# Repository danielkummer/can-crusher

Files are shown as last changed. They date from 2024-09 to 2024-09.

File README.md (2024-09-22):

# Can Crusher

This can crusher uses a liner motor to slowly but surely crush your tin can.

## Bill of Materials

### Screws
* 17x M3 screws (different lengths)
* 10x M4 screws 10mm
* 4x M5 screws 15mm

### Hardware
* 1x Linear shaft
* 1x Stepper motor with gearbox
* 2x push button sensors
* 1x RGB LED push button
* 1x WS2811S led driver
* 1x stepper motor driver 2A
* 1x Arduino Nano every
* 1x 12V 2A power supply
* 1x power supply connector
* connection cables of different lengths

### Stepper Motor

You'll need a stepper motor with a gearbox to produce a lot of torque.
I've found one here: https://eu.robotshop.com/de/products/12v-17a-667-oz-in-nema-17-bipolarer-schrittmotor 

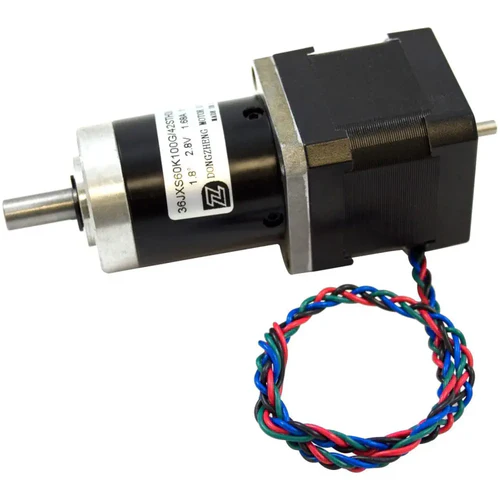
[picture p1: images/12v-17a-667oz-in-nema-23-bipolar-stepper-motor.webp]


It's a 12 V, 1,7 A, 667 oz-in NEMA-17 bipolar stepper motor with a 991044/2057 :1 planetary gear ratio.
The important metric however is the **48kg/cm torque** it can produce.

### Linear shaft

This will be a bit a hassle to find probably. I have found mine here: https://techstudio.ch/products/zeberoxyz-150mm-effektive-lnge-linear-schienenfhrung-kugelumlaufspindel-sfu1605-mit-nema17-schrittmotor-fr-diy-cnc-router-teile-x-y-z-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 

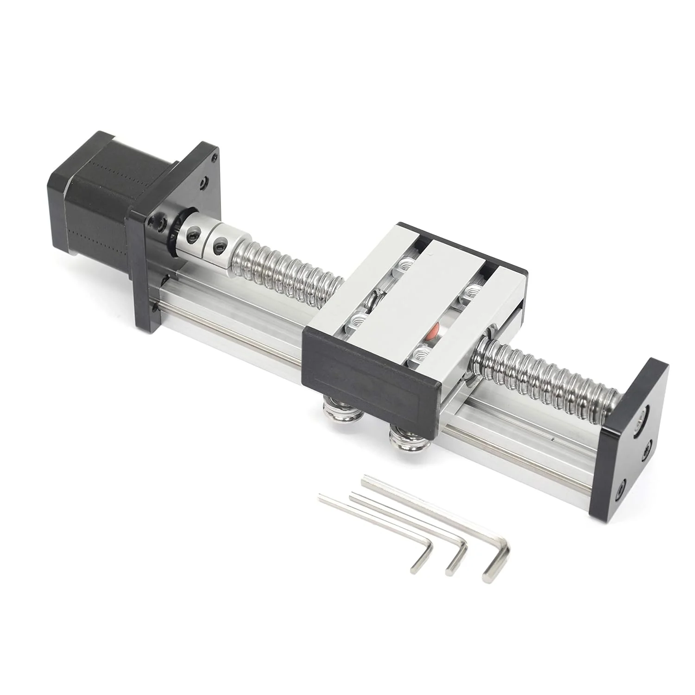
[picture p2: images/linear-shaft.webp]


It has an effective length of 150mm which should be enough for most normal sized tin cans.

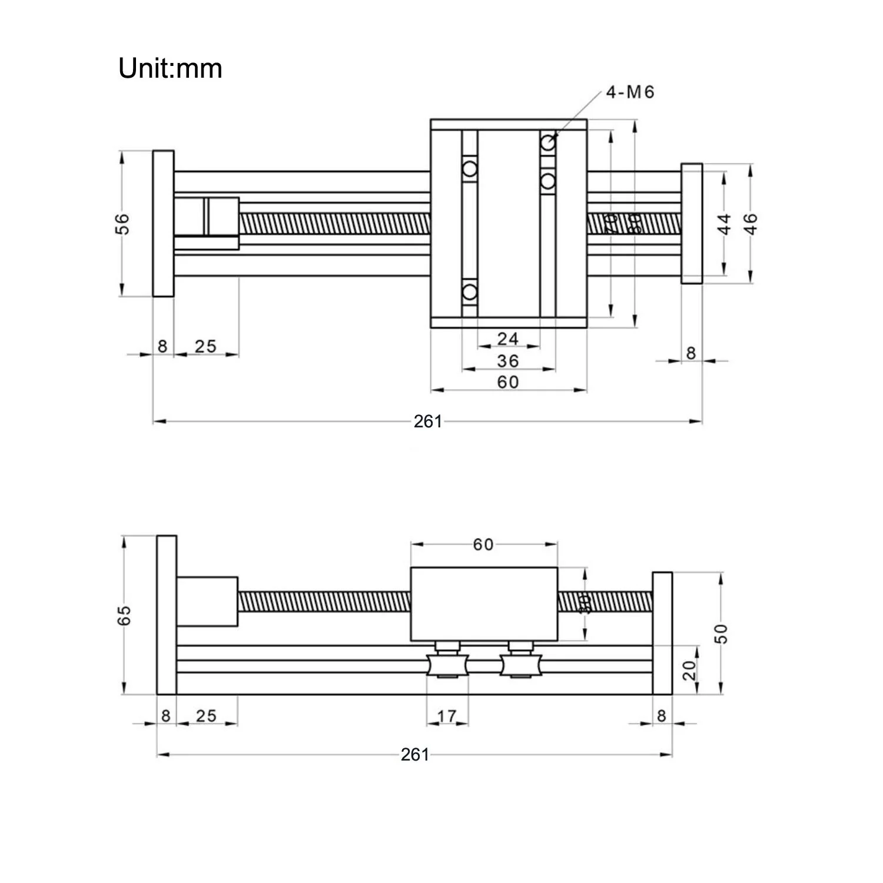
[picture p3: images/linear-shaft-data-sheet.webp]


The shaft came with a Nema 17 stepper motor but it was ungeared and way too weak.

### Push button

The push button is coming from adafruit: https://www.adafruit.com/product/3350 

Diameter: 16mm

### Sensors

I'm using a microswitch breakout board obtained here: https://www.play-zone.ch/de/microswitch-breakout-endstop-active-low.html

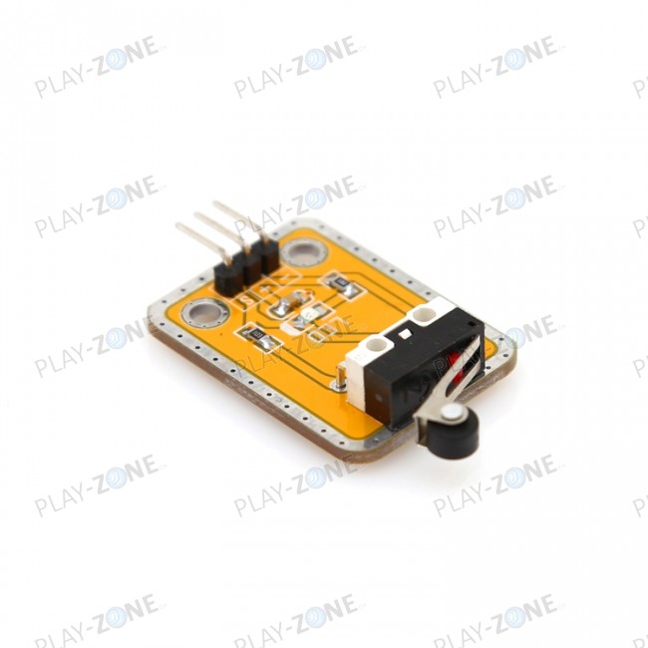
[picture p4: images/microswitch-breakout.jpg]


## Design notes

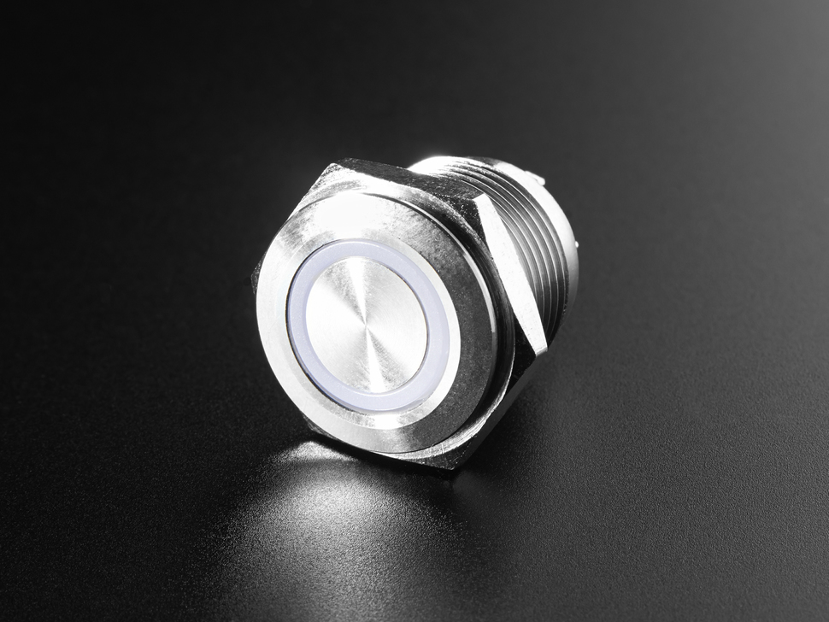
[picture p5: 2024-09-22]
images/metal-pushbutton.jpg

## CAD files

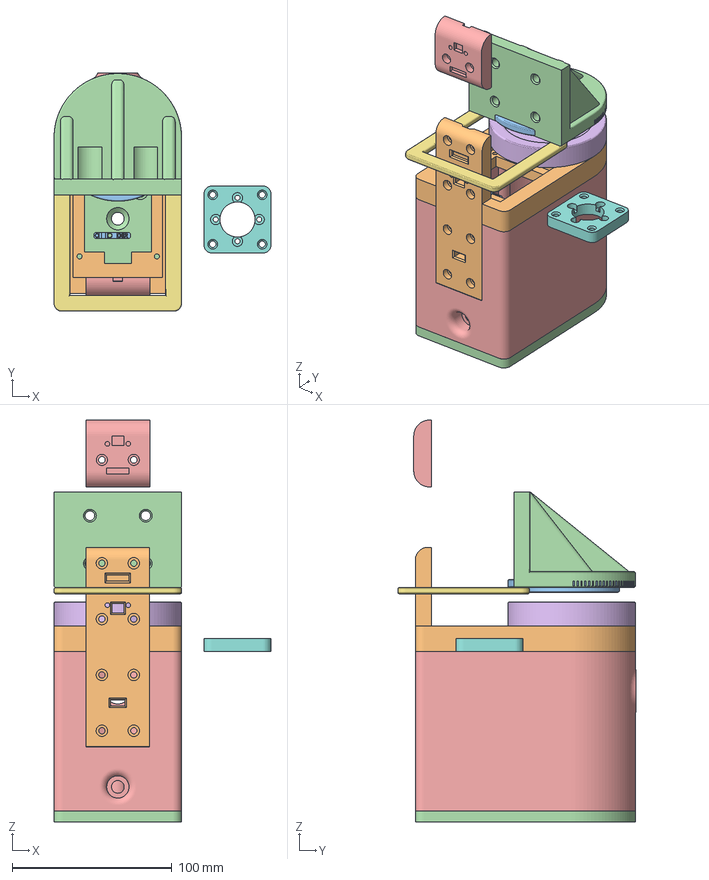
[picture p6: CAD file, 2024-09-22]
3d-files/CanCrusherWithLinerMotor.3mf
136.0 x 149.5 x 252.0 mm
ArduinoClamp
BackFastener
Bottom
Casing
CrusherPlate
CrusherPlateSensorBack
MotorAdapter
MotorDriverClamp
MotorMounting
Tag
TopCrusher
TopSensorHolder

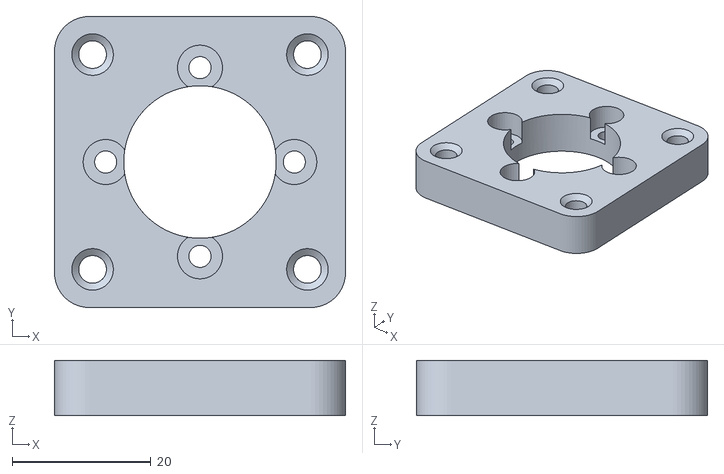
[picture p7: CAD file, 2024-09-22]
print-files/MotorAdapter.stl
42.0 x 42.0 x 8.00

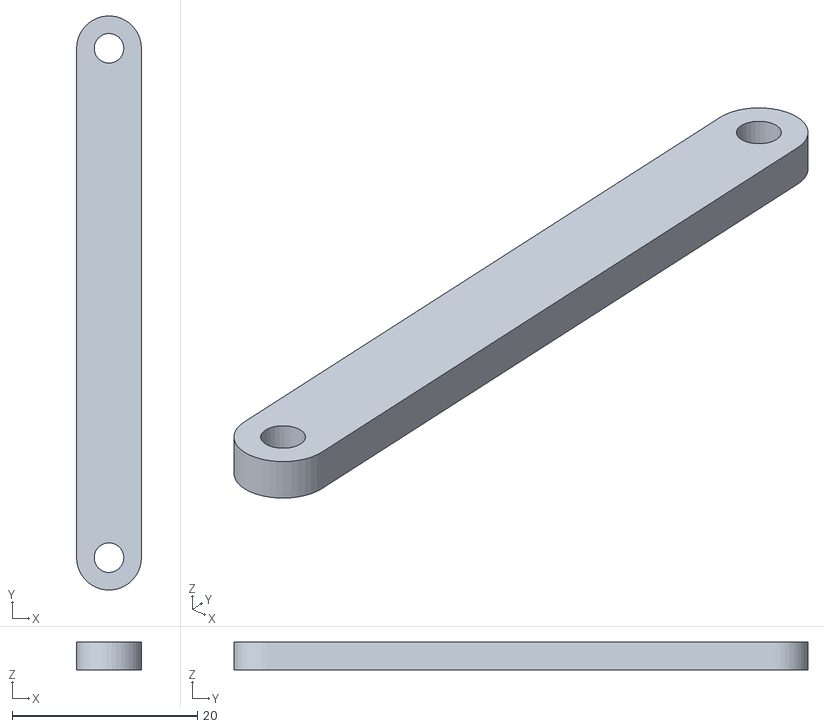
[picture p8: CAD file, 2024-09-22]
print-files/ArduinoClamp.stl
7.00 x 62.0 x 3.00

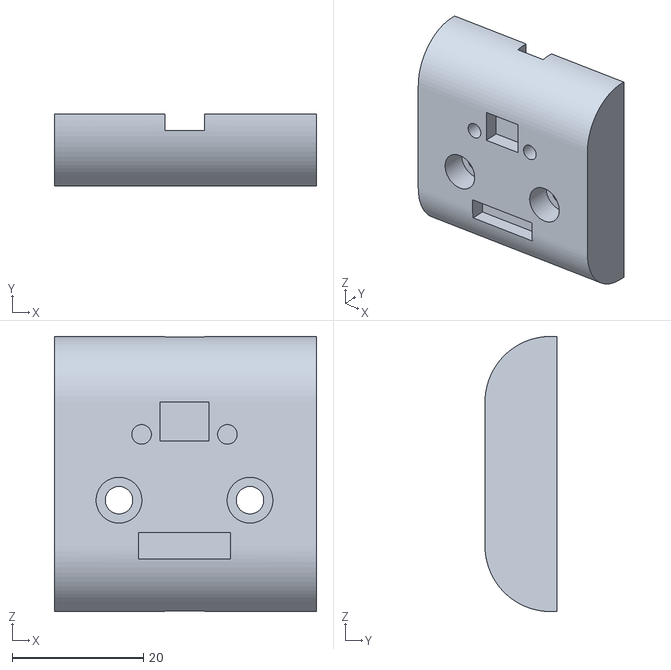
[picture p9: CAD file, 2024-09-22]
print-files/TopSensorHolder.stl
40.0 x 11.0 x 42.0

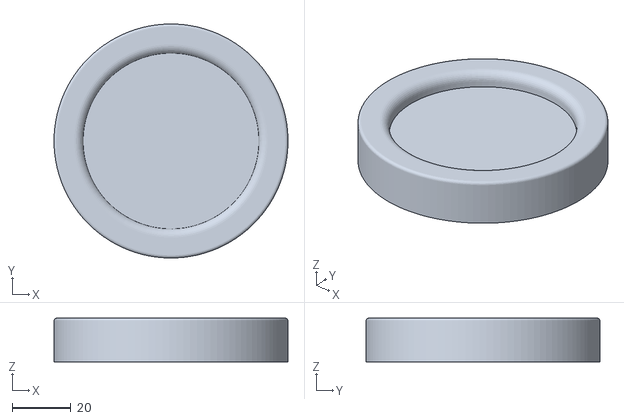
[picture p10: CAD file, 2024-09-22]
print-files/CrusherPlate.stl
80.0 x 80.0 x 15.0

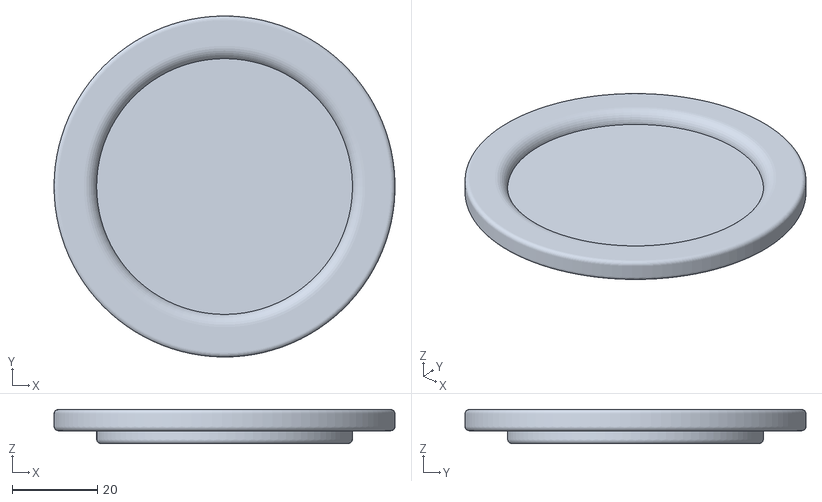
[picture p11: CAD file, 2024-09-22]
print-files/CrusherCup.stl
80.0 x 80.0 x 8.00

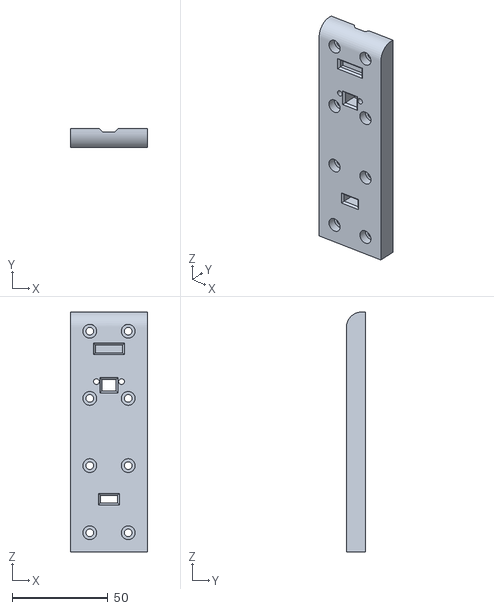
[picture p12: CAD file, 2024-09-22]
print-files/BackFastener.stl
40.0 x 10.0 x 125.0

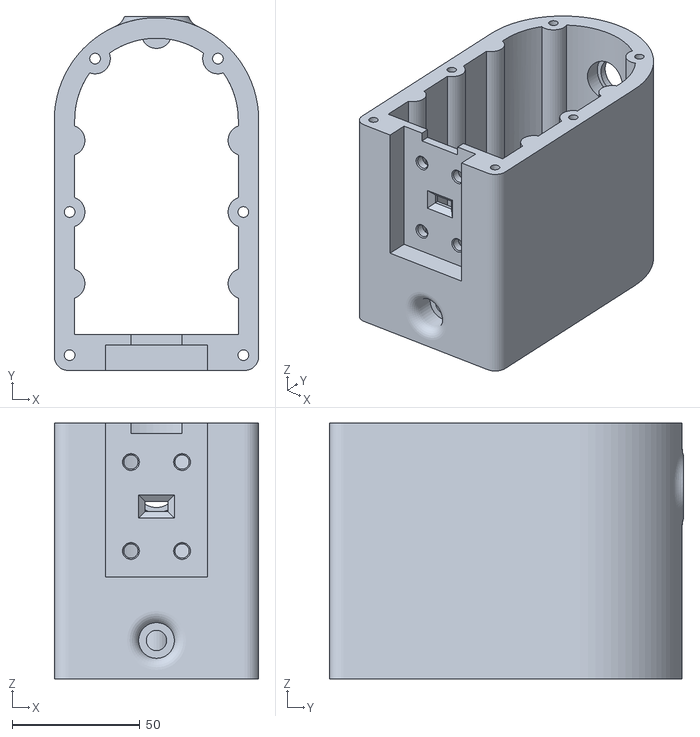
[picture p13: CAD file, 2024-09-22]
print-files/Casing.stl
80.0 x 138.5 x 100.0

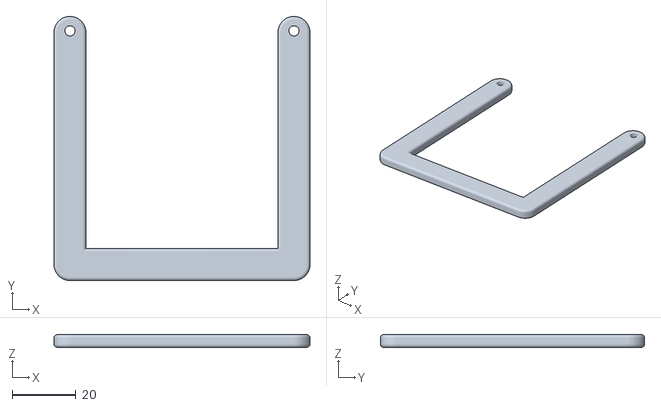
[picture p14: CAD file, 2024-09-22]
print-files/CrusherPlateSensorBack.stl
80.0 x 82.5 x 4.00

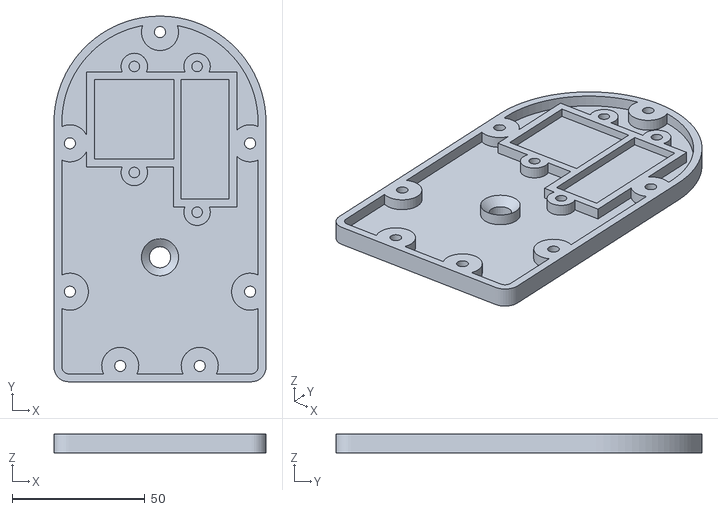
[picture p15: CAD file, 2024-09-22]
print-files/Bottom.stl
80.0 x 138.0 x 7.00

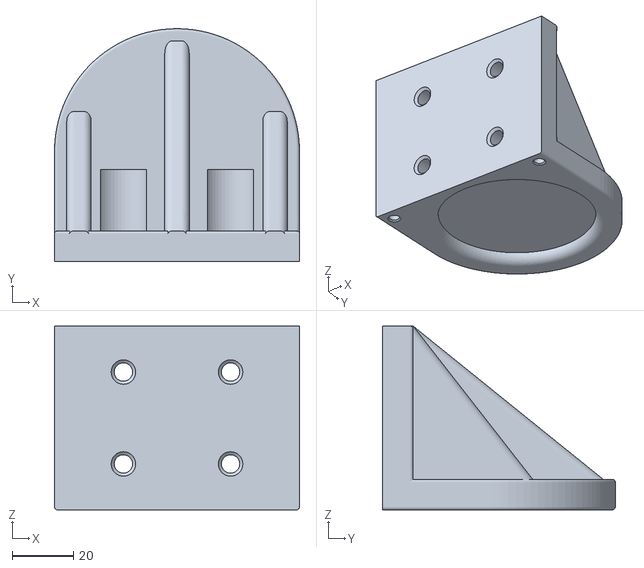
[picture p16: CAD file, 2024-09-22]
print-files/TopCrusher.stl
80.0 x 76.0 x 60.0

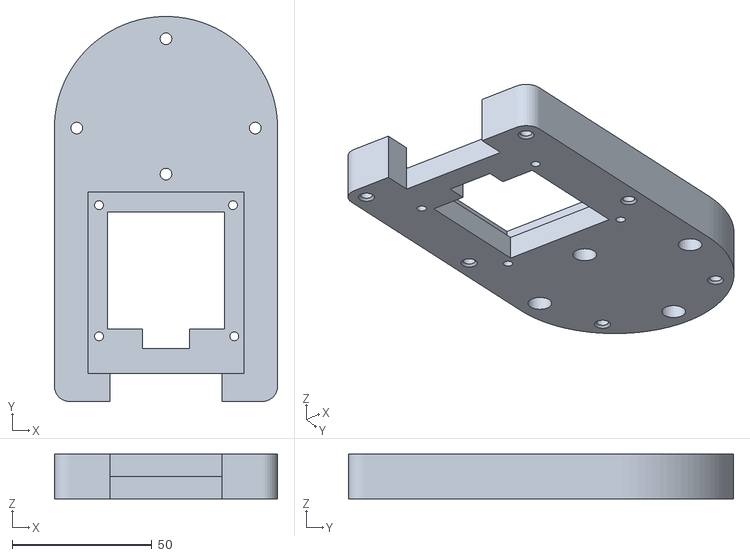
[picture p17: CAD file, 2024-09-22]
print-files/MotorMounting.stl
80.0 x 138.0 x 16.0

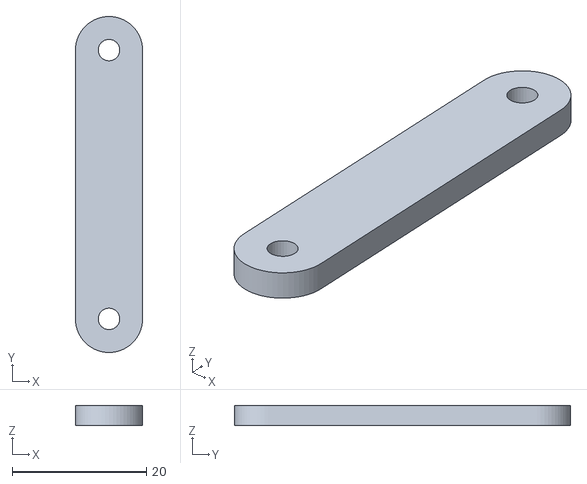
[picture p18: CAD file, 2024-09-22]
print-files/MotorDriverClamp.stl
10.0 x 50.0 x 3.00

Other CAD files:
3d-files/CanCrusherWithLinerMotor.f3d
3d-files/CanCrusherWithLinerMotor.obj

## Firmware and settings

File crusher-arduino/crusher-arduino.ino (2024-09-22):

#include <OneButton.h>      //https://github.com/mathertel/OneButton
#include <AccelStepper.h>   //https://www.airspayce.com/mikem/arduino/AccelStepper/index.html
#include "FastLED.h"        //https://github.com/FastLED/FastLED
#include "LedEffects.h"


// PIN DEFINITIONS
#define BUTTON 11
#define TOP_STOP_SENSOR 10
#define BOTTOM_STOP_SENSOR 9

#define MOTOR_STEP 8
#define MOTOR_DIRECTION 7

#define LED_PIN 12
#define NUM_LEDS 1


// MOTOR DEFINITIONS

#define MAX_SPEED 1850
#define SPEED 1800          // This is the maximum speed the motor is capable of
#define RESET_OFFSET 3000   //Moving the crusher a bit away from the sensor

#define BRIGHTNESS 255      // Default LED brightness

CRGB leds[NUM_LEDS];
LedEffects ledEffects(leds, NUM_LEDS);

AccelStepper stepper(AccelStepper::DRIVER, MOTOR_STEP, MOTOR_DIRECTION);

bool buttonPressed, buttonLongPressed, topSensorTriggered, bottomSensorTriggered;

enum State {
  RESET,
  MOVE_TO_IDLE,
  IDLE,
  CRUSHING,
  STOP
};

OneButton topSensor = OneButton(
  TOP_STOP_SENSOR,  // Input pin for the button
  true,             // Button is active LOW
  true              // Enable internal pull-up resistor
);

OneButton bottomSensor = OneButton(
  BOTTOM_STOP_SENSOR,  // Input pin for the button
  true,                // Button is active LOW
  true                 // Enable internal pull-up resistor
);

OneButton btn = OneButton(
  BUTTON,  // Input pin for the button
  true,    // Button is active high
  true     // Disable internal pull-up resistor
);

/**
* Read boolean value and reset it after reading. This is needed to combine OneButton and StateMachine
*/
bool sensorTriggered(bool &sensorTriggered) {
  bool wasTriggered = sensorTriggered;
  sensorTriggered = false;
  return wasTriggered;
}

// Wrapper functions for each sensor, we need this "abstraction" to make it work with the state machine implementation
bool checkTopSensorTriggered() {
  return sensorTriggered(topSensorTriggered);
}

bool checkBottomSensorTriggered() {
  return sensorTriggered(bottomSensorTriggered);
}

bool checkButtonPressed() {
  return sensorTriggered(buttonPressed);
}

bool checkButtonLongPressed() {
  return sensorTriggered(buttonLongPressed);
}

State currentState = RESET;
State previousState = RESET;

bool executeOnce = true;

long endPosition = 485000;  //

// Function to change state, ensuring the transition only happens once
void changeState(State newState) {
  if (newState != currentState) {
    previousState = currentState;
    currentState = newState;
    executeOnce = true;  // Reset executeOnce flag when entering a new state
    Serial.print("Entering state: ");
    Serial.println(currentState);  // Debugging output
  }
}

// Main function to handle states and execute logic
void handleState() {
  switch (currentState) {
    case RESET:
      if (executeOnce) {
        // Code to run when entering RESET state
        Serial.println("# Resetting");
        stepper.setSpeed(SPEED);
        stepper.moveTo(-endPosition);
        executeOnce = false;  // Ensure this block runs only once

        Serial.print("Current Position: ");
        Serial.println(stepper.currentPosition());  // Check current position

        Serial.print("Distance to go Position: ");
        Serial.println(stepper.distanceToGo());  // Check current position
      }
      // Handle pulse effect
      ledEffects.pulse(CRGB::Blue, 1500);

      // Move the motor to the idle position
      if (stepper.distanceToGo() != 0) {
        stepper.run();
      }

      // Transition to MOVE_TO_IDLE if the top sensor is triggered
      if (checkTopSensorTriggered()) {
        stepper.stop();
        Serial.print("Reached top sensor, current position before resetting it: ");
        Serial.println(stepper.currentPosition());
        stepper.setCurrentPosition(0);
        changeState(MOVE_TO_IDLE);
      }

      // Transition to STOP if the button is pressed
      if (checkButtonPressed()) {
        changeState(STOP);
      }
      break;

    case MOVE_TO_IDLE:
      if (executeOnce) {
        Serial.println("# Moving to idling position");
        stepper.setSpeed(SPEED);
        stepper.setCurrentPosition(0);
        stepper.moveTo(RESET_OFFSET);

        executeOnce = false;  // Ensure this block runs only once

        Serial.print("Current Position: ");
        Serial.println(stepper.currentPosition());  // Check current position

        Serial.print("Distance to go Position: ");
        Serial.println(stepper.distanceToGo());  // Check current position
      }
      // Run pulse effect
      ledEffects.pulse(CRGB::Blue, 500);

      // Move the motor to the idle position
      if (stepper.distanceToGo() != 0) {
        stepper.run();
      } else {
        // Transition to IDLE when the motor reaches the idle position
        Serial.println("Reached the idle position.");
        changeState(IDLE);
      }
      break;

    case IDLE:
      if (executeOnce) {
        Serial.println("# Idling");
        stepper.stop();       // Stop motor when entering idle
        executeOnce = false;  // Ensure this block runs only once
      }
      ledEffects.rainbow(20);

      // Transition to CRUSHING state if button is pressed
      if (checkButtonPressed()) {
        changeState(CRUSHING);
      }
      break;

    case CRUSHING:
      if (executeOnce) {
        Serial.println("# Crushing");
        stepper.setSpeed(SPEED);
        stepper.moveTo(endPosition);
        executeOnce = false;  // Ensure this block runs only once

        Serial.print("Current Position: ");
        Serial.println(stepper.currentPosition());  // Check current position

        Serial.print("Distance to go Position: ");
        Serial.println(stepper.distanceToGo());  // Check current position
      }
      ledEffects.pulse(CRGB::Orange, 1500);

      // Move the motor to the idle position
      if (stepper.distanceToGo() != 0) {
        stepper.run();
      } else {
        Serial.print("Did not reach bottom sensor but exhausted travel path");
        stepper.stop();
        changeState(RESET);
      }

      // Transition to RESET if bottom sensor is triggered
      if (checkBottomSensorTriggered()) {
        Serial.print("Reached bottom sensor, current position before reset: ");
        Serial.println(stepper.currentPosition());
        endPosition = stepper.currentPosition();  //update the end position now that we know it for sure
        stepper.stop();
        changeState(RESET);
      }

      // Transition to STOP if button is pressed
      if (checkButtonPressed()) {
        stepper.stop();
        changeState(STOP);
      }
      break;

    case STOP:
      if (executeOnce) {
        Serial.println("# Stopped, waiting for button actions");
        stepper.stop();       // Stop motor when entering STOP state
        executeOnce = false;  // Ensure this block runs only once
      }
      ledEffects.pulse(CRGB::Green, 1000);

      // Transition to RESET if button is pressed
      if (checkButtonPressed()) {
        stepper.setSpeed(SPEED);
        stepper.moveTo(-endPosition);
        changeState(RESET);
      }

      // Transition to CRUSHING if long press detected
      if (checkButtonLongPressed()) {
        stepper.setSpeed(SPEED);
        stepper.moveTo(endPosition);
        changeState(CRUSHING);
      }
      break;
  }
}

void setup() {

  Serial.begin(9600);
  Serial.println("# Startup");

  Serial.println("Configuring LED");
  FastLED.addLeds<WS2811, LED_PIN, RGB>(leds, NUM_LEDS);

  Serial.println("Configuring Stepper");
  stepper.setMaxSpeed(MAX_SPEED);  // Max speed (steps/second)
  stepper.setAcceleration(1000);   // Acceleration (steps/second^2)
  stepper.setCurrentPosition(0);

  Serial.println("Configuring Button and Sensors");
  btn.attachClick([]() {
    Serial.println("Clicked!");
    buttonPressed = true;
  });
  btn.attachLongPressStart([]() {
    Serial.println("Long Press Start!");
    buttonLongPressed = true;
  });
  topSensor.attachPress([]() {
    Serial.println("Top sensor triggered!");
    topSensorTriggered = true;
  });
  bottomSensor.attachPress([]() {
    Serial.println("Bottom sensor triggered!");
    bottomSensorTriggered = true;
  });
  changeState(RESET);
}


void loop() {
  btn.tick();
  bottomSensor.tick();
  topSensor.tick();
  
  handleState();

  // Update the LEDs as needed (reduce FastLED.show() calls for performance)
  static unsigned long lastLedUpdate = 0;
  const unsigned long ledUpdateInterval = 50;  // Update every 50ms
  unsigned long currentMillis = millis();
  if (currentMillis - lastLedUpdate >= ledUpdateInterval) {
    lastLedUpdate = currentMillis;
    FastLED.show();
  }
}

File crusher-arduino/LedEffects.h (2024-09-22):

#ifndef LED_EFFECTS_H
#define LED_EFFECTS_H

#include <FastLED.h>

class LedEffects {
  private:
    CRGB* leds;          // Pointer to the LED array
    int numLeds;         // Number of LEDs
    int brightness;      // Current brightness level for effects
    unsigned long effectStartTime;  // When an effect (like rainbow) started
    bool rainbowInitialized;        // To ensure the rainbow starts correctly
    uint8_t hue;         // For rainbow effect: tracks hue value

  public:
    // Constructor to initialize the LED array and number of LEDs
    LedEffects(CRGB* leds, int numLeds) {
      this->leds = leds;
      this->numLeds = numLeds;
      this->brightness = 255;        // Default brightness set to full
      this->effectStartTime = 0;
      this->rainbowInitialized = false;
      this->hue = 0;                 // Start hue at 0 for rainbow effect
    }

    // Pulse effect: smoothly increase/decrease brightness of a given color, with a specified pulse duration
    void pulse(CRGB color, unsigned long pulseDuration) {
    unsigned long currentTime = millis();
    
    // If this is the first call, initialize the pulse start time
    if (!rainbowInitialized) {
        effectStartTime = currentTime;
        rainbowInitialized = true;
    }

    // Calculate elapsed time since the pulse started
    unsigned long elapsedTime = currentTime - effectStartTime;
    unsigned long halfPulseDuration = pulseDuration >> 1;  // Faster division by 2 using bit shift

    // Reset the pulse if it completed the full duration
    if (elapsedTime >= pulseDuration) {
        effectStartTime = currentTime;  // Restart the pulse
        elapsedTime = 0;
    }

    // Instead of using map(), we'll directly calculate brightness linearly
    int brightness;
    if (elapsedTime <= halfPulseDuration) {
        // Fade-in: brightness increases linearly from 0 to 255
        brightness = (elapsedTime * 255) / halfPulseDuration;
    } else {
        // Fade-out: brightness decreases linearly from 255 to 0
        brightness = ((pulseDuration - elapsedTime) * 255) / halfPulseDuration;
    }

    // Set brightness for each LED
    for (int i = 0; i < numLeds; i++) {
        leds[i] = color;
        leds[i].nscale8(brightness);  // Scale the color based on calculated brightness
    }    
}


    // Rainbow effect: cycle through rainbow colors at a given speed
    void rainbow(unsigned long speedDelay) {
      unsigned long currentTime = millis();

      // Initialize rainbow effect start time only once
      if (!rainbowInitialized) {
        effectStartTime = currentTime;
        rainbowInitialized = true;
      }

      // Check if it's time to update the rainbow
      if (currentTime - effectStartTime >= speedDelay) {
        effectStartTime = currentTime;  // Update the start time

        // Cycle through hues for a rainbow effect
        for (int i = 0; i < numLeds; i++) {
          leds[i] = CHSV(hue + (i * 256 / numLeds), 255, brightness);  // Hue shifts across LEDs
        }

        // Increment hue for smooth transition
        hue++;
        if (hue == 255) {
          hue = 0;  // Loop back to the start of the rainbow
        }
      }
    }

    // Solid color effect
    void solidColor(CRGB color) {
      for (int i = 0; i < numLeds; i++) {
        leds[i] = color;
      }
    }
};

#endif
